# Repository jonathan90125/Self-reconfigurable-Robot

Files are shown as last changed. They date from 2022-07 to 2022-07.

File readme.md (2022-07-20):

# Self-reconfigurable Robot

## PHASE 1

This is the project I did for the "College Students Innovation and Entrepreneurship Competition" in China. And it was certificated as a province level project in the competition. 

### Background

Modular self-reconfigurable robots (MSRR) are robots that consist of many relatively simple individual robots which can cooperate together by changing their configuration according to different tasks. Many researches as shown below about this topic have been done in recent years, trying to achieve a practical robotic structure.  

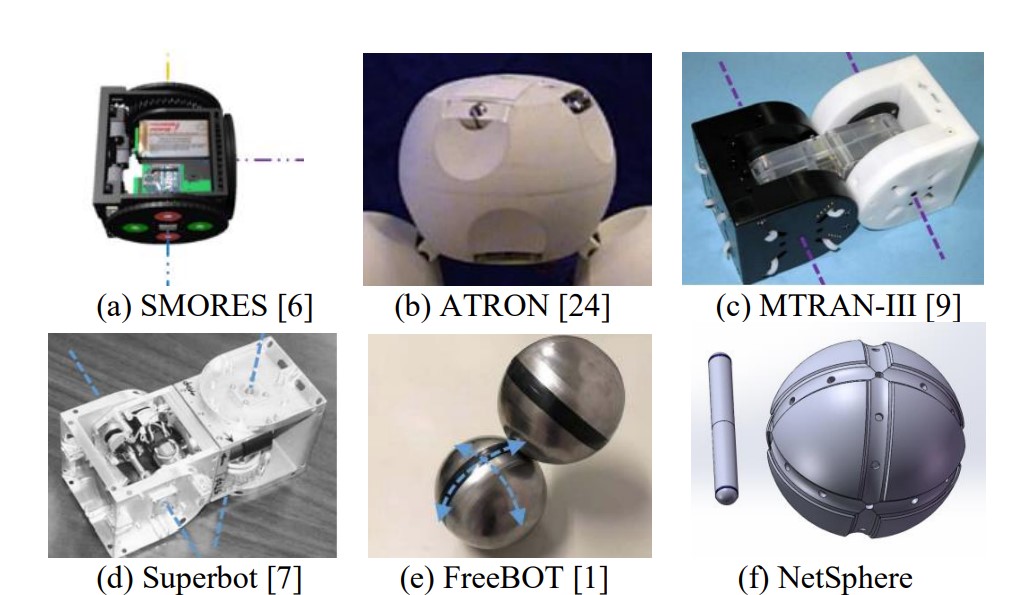
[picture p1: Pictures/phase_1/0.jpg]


### Introduction

In my opinion, former MSRR's major problem is the limited number of connectors on each individual robots. In order to solve that problem, I designed my own self-reconfigurable robot which contains two types of modules. The sphere modules can be connected by the stick modules to form various three-dimensional shapes. Sphere module contains ferromagnetic spherical shell and an internal actuating system. The remaining space in the shell can be used for electronic components and power supply (only one of eight sections is illustrated in the graph). An additional passive docking ports is on the shell which are used to cooperate with stick module. The stick module is equipped with two magnets and two active docking ports on both ends. The remaining space in the middle of the module is used for two motors which can actuate the docking ports. The internal  electronic components for each modules are very simple as shown in the graph below.

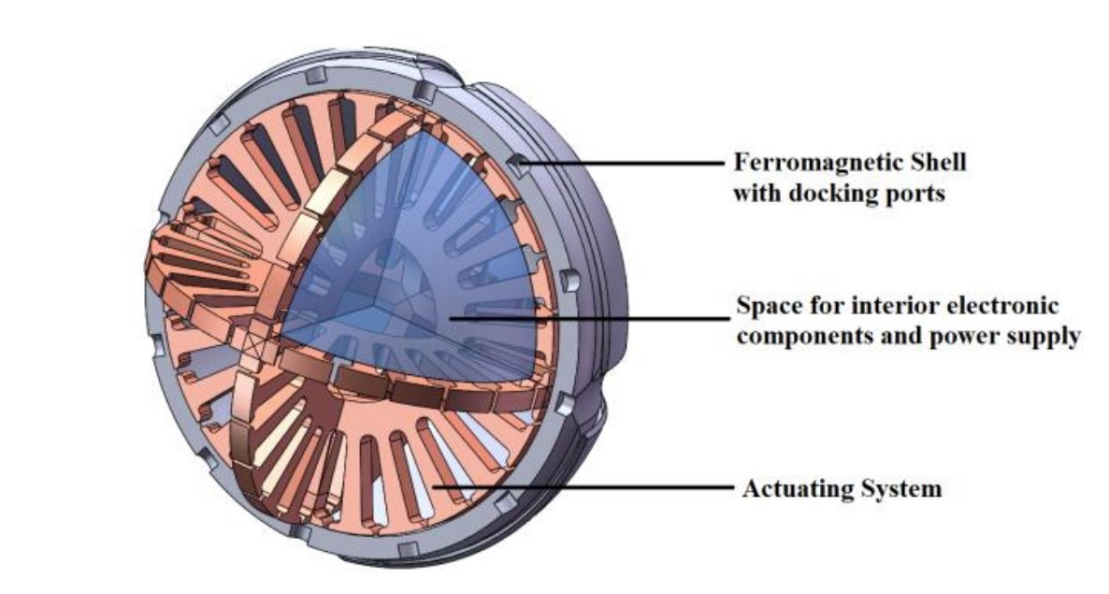
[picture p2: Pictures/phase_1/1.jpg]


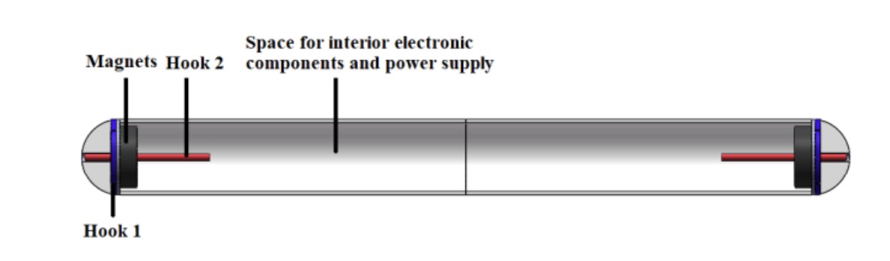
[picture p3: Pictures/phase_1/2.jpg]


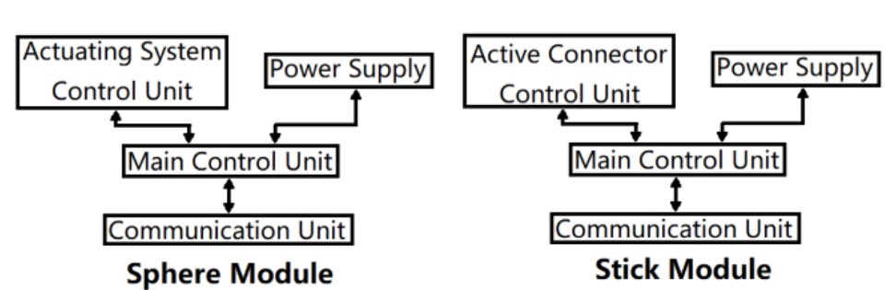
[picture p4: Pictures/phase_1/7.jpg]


### Actuating System

Figures below show the structure of the actuating system. There are three orthogonal circles inside the shell with 24 electromagnets on each circle, and each circle’s structure is similar to the stator of motor. All the electromagnets inside the sphere module are arranged  to control the magnetic force distribution of the spherical shell, which in turn can drive the magnets  at the end of the stick module to move on the surface of the sphere.

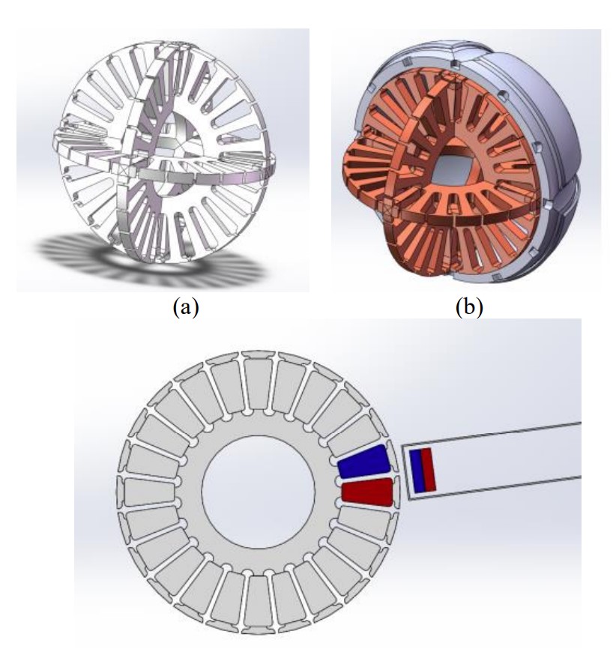
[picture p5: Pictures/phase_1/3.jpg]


### Docking System

There are two types of docking ports, the active docking ports of stick module and passive docking ports of sphere module. The hooks of active connector which is implemented inside the stick module have three states to provide suitable stability for the system. There are two different hooks in the active connector, one is to keep the stick module strongly connected to the surface of the sphere, the other is used to keep the stick locked at a certain position. There are three conditions of the two hooks, both nonactivated, only hook 1 activated, both activated, which means hook 2 can only be activated when 1 is activated. Hence, only one motor is needed to control both hooks since they are not independent.

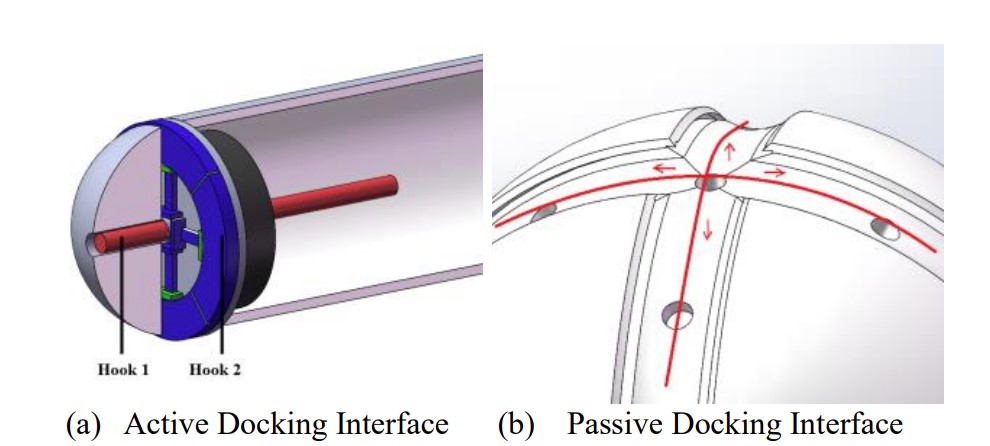
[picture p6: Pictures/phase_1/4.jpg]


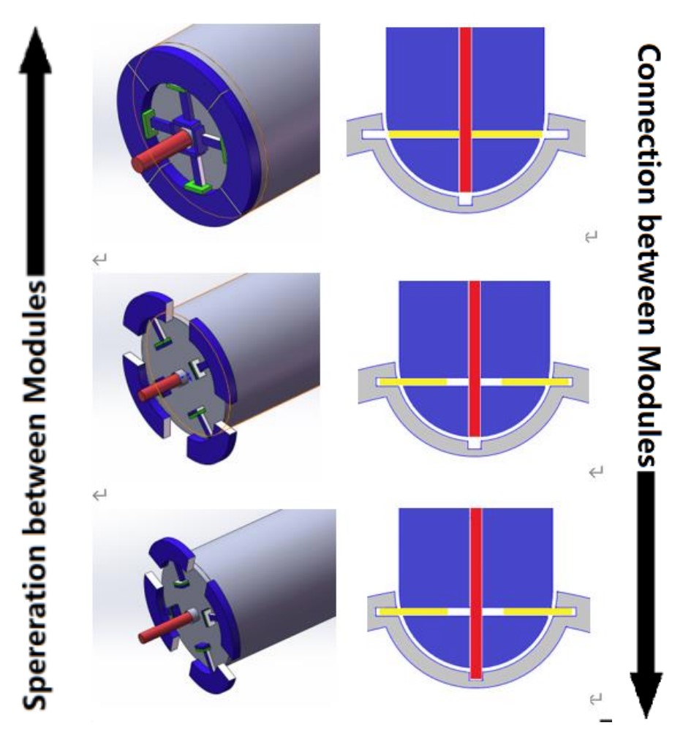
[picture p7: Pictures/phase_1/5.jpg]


### Connection of Individual modules

All the modules are meaningless unless they can cooperate together to form a holistic structure and solve problems cooperatively. So the algorithm to manage all the separate modules together to work together is also an important part of the design. Currently, the proposed strategy of connecting all the modules together can be arranged into 4 phases:

*1)*   *To from the simplest structure that is able to move independently. (a)*

*2)*   *Using these structures to gather more modules to achieve a relatively stable system. (b)*

*3)*   *Using the small systems that have been formed to gather modules. (c)*

*4)*   *Combining all the small systems together to obtain the final structure we desire.* 

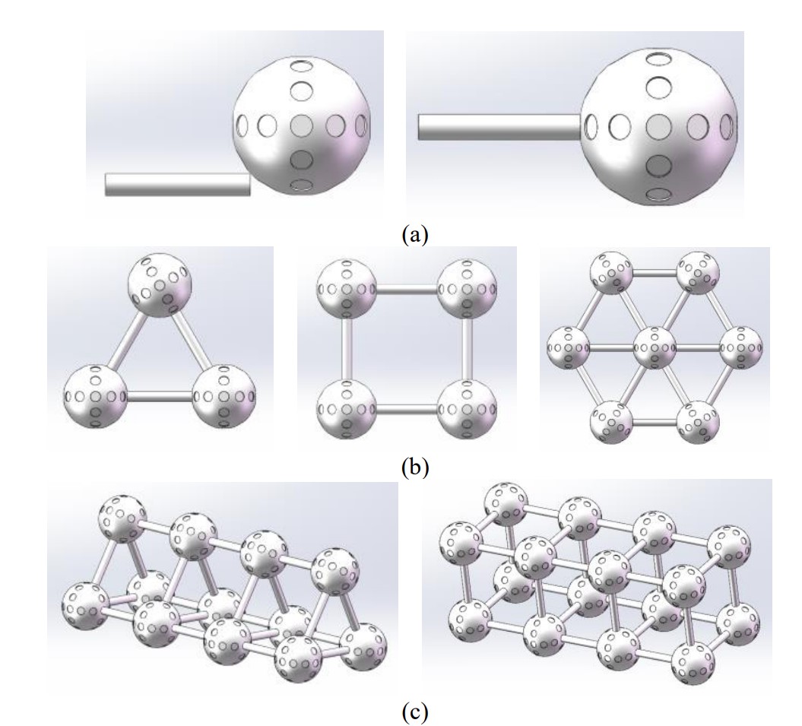
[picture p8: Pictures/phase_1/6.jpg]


### Implement

Some basic tests have been implemented to verify the feasibility of the actuating mechanism. Since the whole structure can be considered as three orthogonal stators and the electromagnets on each stator have little influence to other stators, the feasibility can be test on just one stator. A very preliminary experiment's devices are shown in figure below. The iron core of the prototype is using a stator which is made for motor. Its diameter is 40mm, height is 20mm, number of slots is 12. The diameter of varnished wire is 0.21 which could be much smaller to improve the performance significantly. Since the power dissipation can be reduced because no extra resistance is needed to constrain the current any more. On each tooth of the stator, we put an independent coil on it. The electronics in this testing device is very simple, using a STM32F103C8T6 to control all the independent coils, a ZigBee module CC2530 to communicate with upper computer. Some resistance is added to restrain the current inside the coil. A 12v battery is used to provide power for the coils. A voltage stabilization module AMS1117 is used to provide 3.3v power source for controlling circuit. A simple upper computer program has also been written to control each coil. 

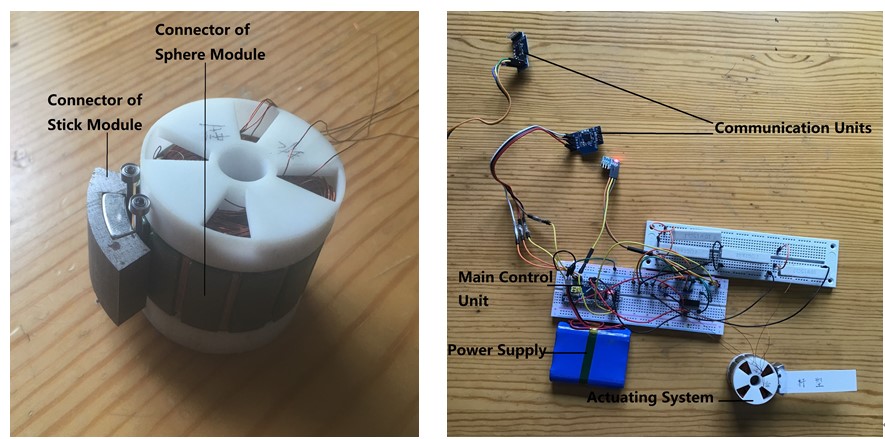
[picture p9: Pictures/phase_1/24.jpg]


## PHASE 2

Further development is carried out during my internship at CUHK's AI and Robotics laboratory. I made modification to the structure and made a functional prototype.

### Modification

The previous mechanical design is very difficult to manufacture especially the array of numerous electromagnets inside the sphere modules. Moreover, the torque provided by the actuator is limited and the connection between modules is not stable enough. To solve these problems, a modification for physical structure is necessary. 

The changed design is much simpler than previous one actually, the sphere module becomes just a hollow ferromagnetic ball and the stick module becomes what shows below. Two driving wheel and an array of magnet on each end and corresponding actuator and other units in between. And these modules can cooperate as shown below to form different shapes.

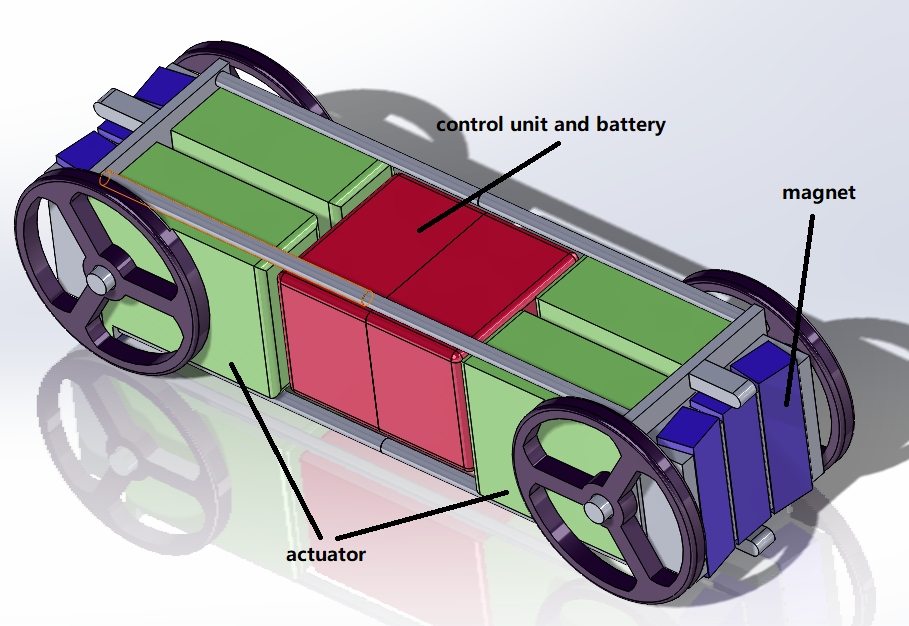
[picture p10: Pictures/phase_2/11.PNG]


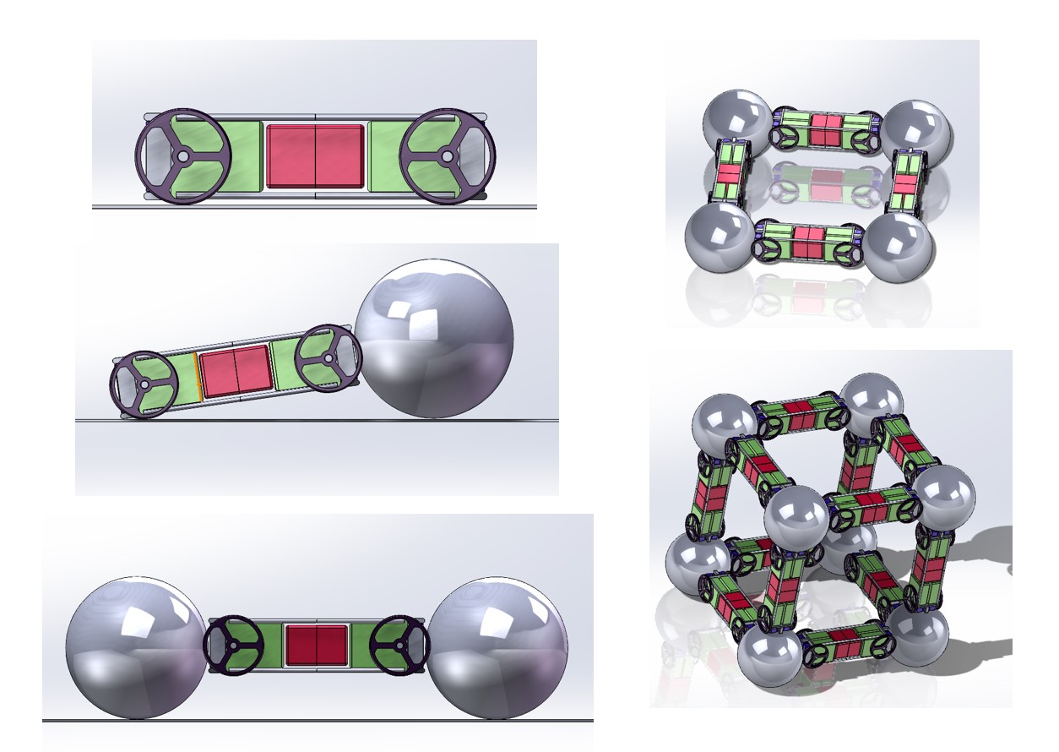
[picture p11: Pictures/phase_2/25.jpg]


### Implement

I firstly made a prototype using 3d printing to get all the components and the attached the wheels, motors and electronic units to it. This prototype can move independently on the ground with just one stick module and two sphere modules. 

After that I optimize the structure by using driving gears to minimize the size of modules. It can be seen that in the following figures, the size has been significantly reduced. 

After all these work, limited by the budget from the lab and I was arranged to other project (an AGV), I didn't make further development for the robots. 

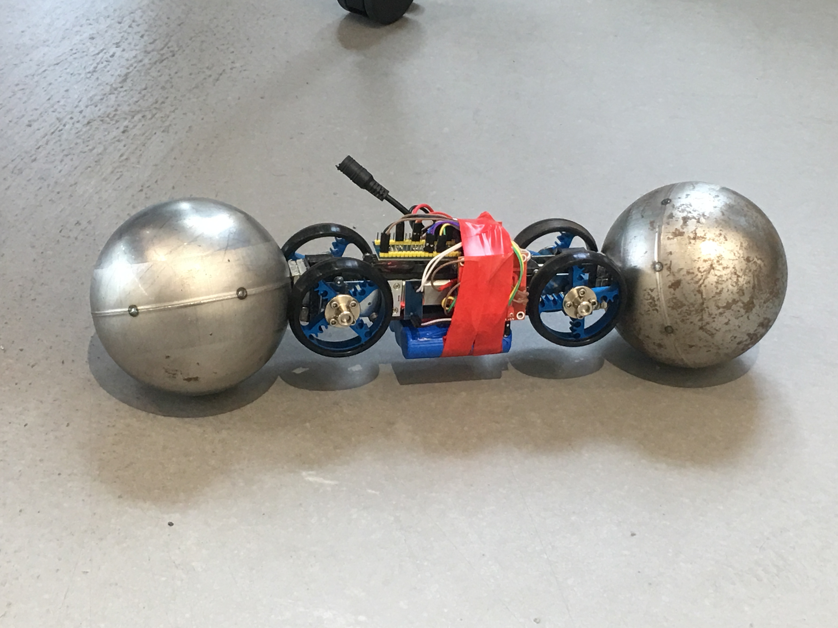
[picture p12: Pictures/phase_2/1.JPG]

<div align=center>
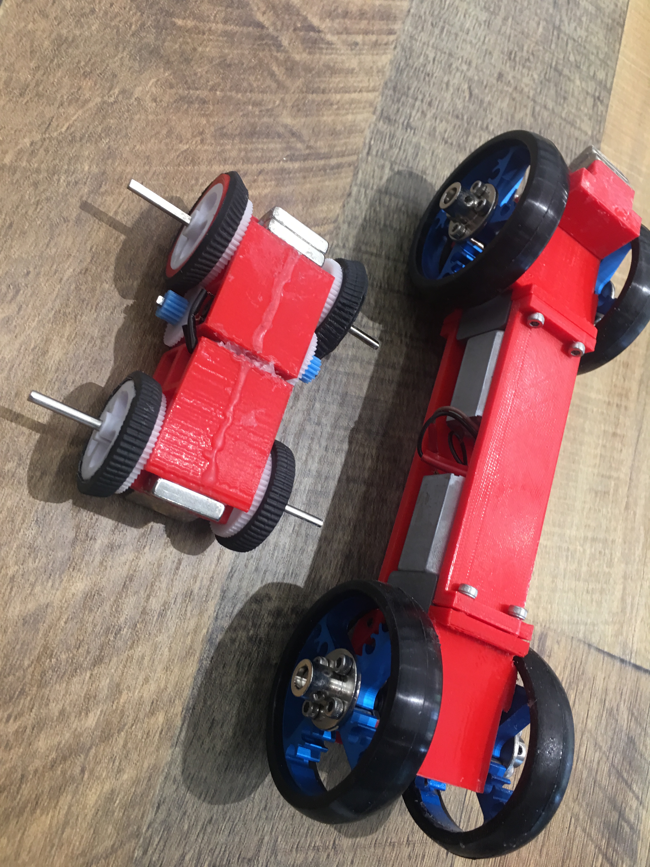
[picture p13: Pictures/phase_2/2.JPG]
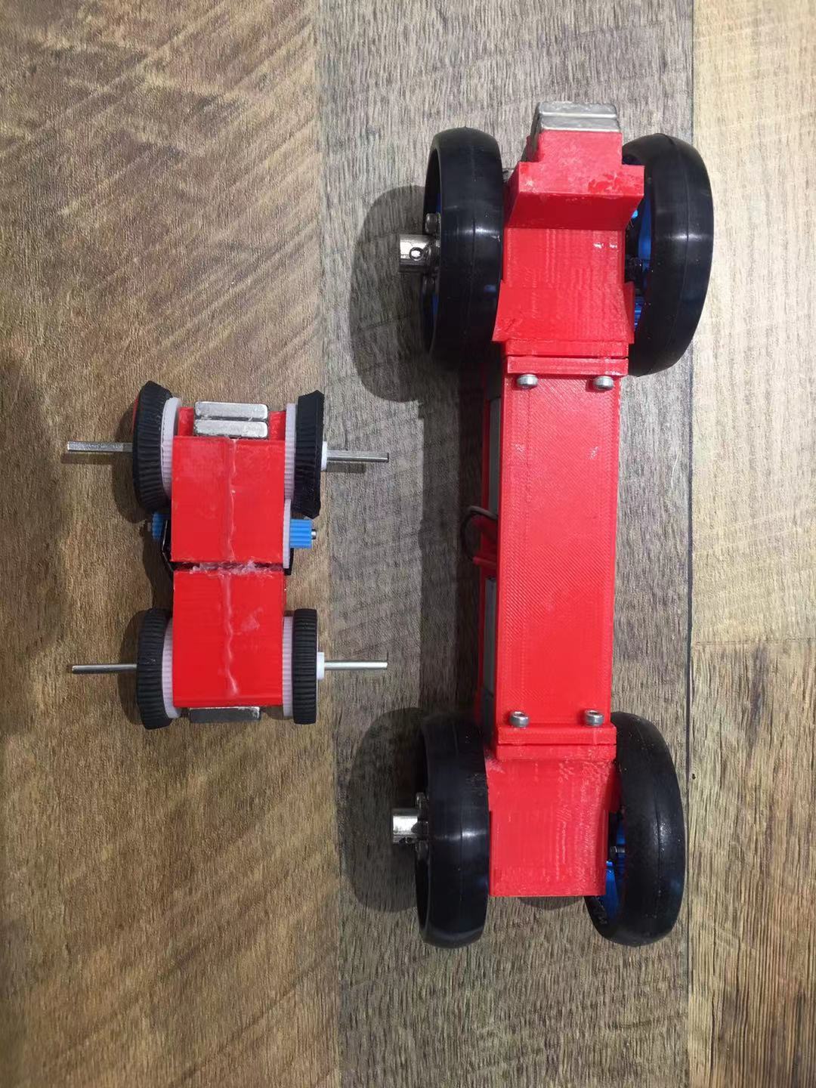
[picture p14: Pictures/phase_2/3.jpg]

</div>
<div align=center>
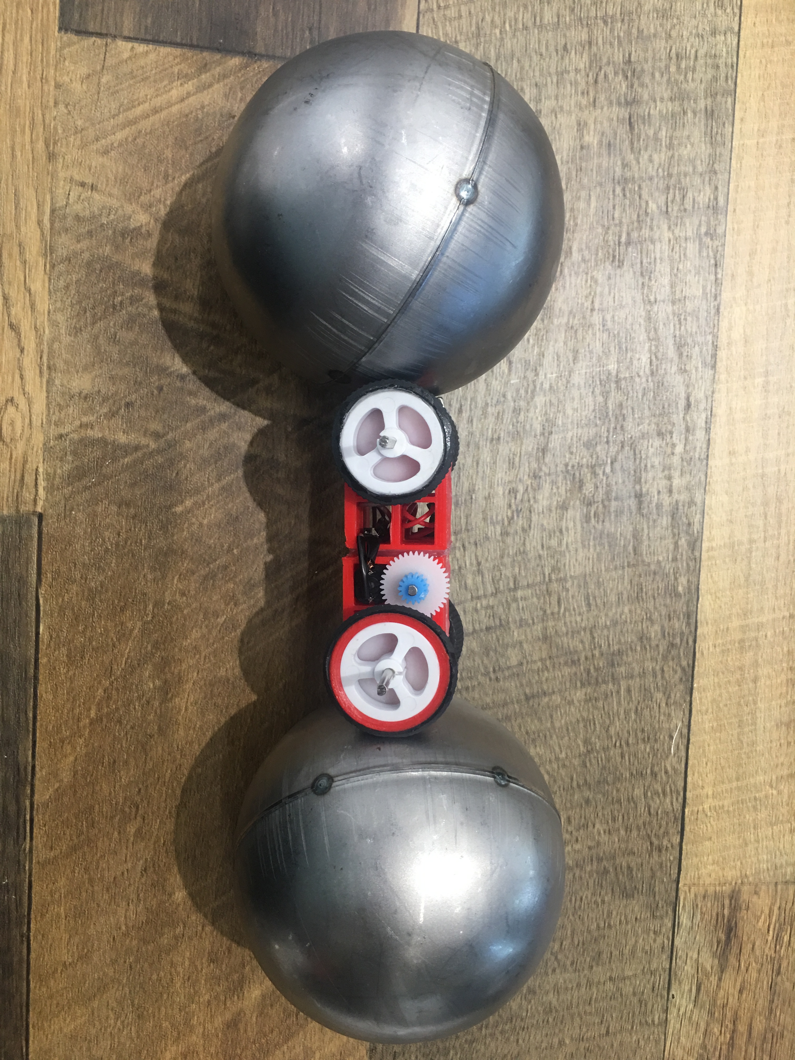
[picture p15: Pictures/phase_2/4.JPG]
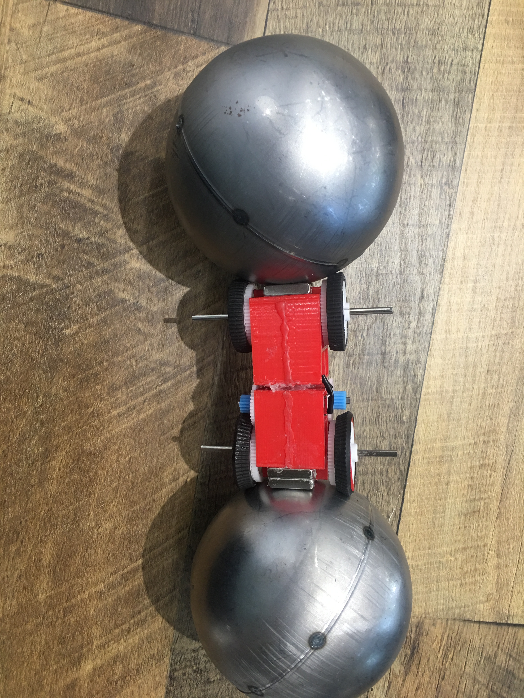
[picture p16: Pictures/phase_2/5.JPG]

</div>

## Future Work

What I was trying to achieve has been implemented by a team from CUHK(Shenzhen) as shown in figures below, details can be found in the paper "FreeSN: A Freeform Strut-node Structured Modular Self-reconfigurable Robot - Design and Implementation". The mechanical design is basically the modification version in phase 2 I illustrated above. In fact, I was working at CUHK(Shenzhen)'s AI and Robotics laboratory at that time when that team is working on this project. I met some members of the team who are also reviewer of my paper that I wrote in phase 1, they gave me some very helpful advice like using simulation to prove the feasibility of the design. But, when I mentioned I was trying to make some modification on the design of the self-reconfigurable robot later, they were doing the similar work simultaneously. They insisted that this was their original idea and they have proof for it.  

Apparently, their prototype is much more elegant and compact than mine. I'm very glad that this idea could be implemented even though not by myself. Since currently the physical prototype has been made, the corresponding controlling algorithm  should to created in the future. Moreover, the size should be minimized and the torque provided by the actuator should be enhanced. 

In my future work, I would like to focus on the controlling algorithms of multi robot instead of innovation about physical structures. Task decomposition, coalition formation and task allocation of multi robot could be interesting researching areas.  

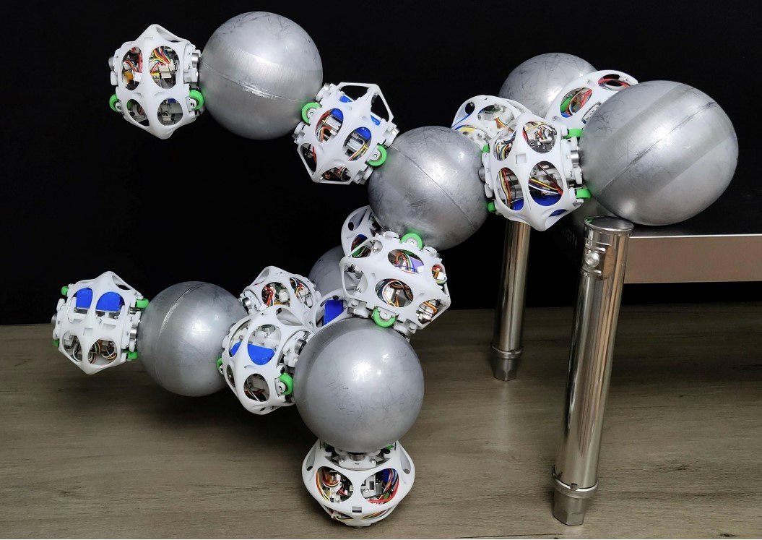
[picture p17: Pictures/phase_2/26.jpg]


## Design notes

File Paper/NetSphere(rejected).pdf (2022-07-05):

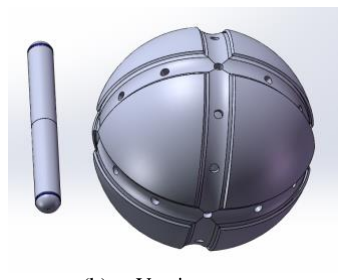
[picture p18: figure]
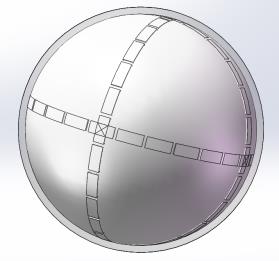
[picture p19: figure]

Abstract—In this paper, a novel design of lattice-like modular self-reconfigurable robot named “NetSphere” which does not apply traditional motor as its actuator will be described. The module of NetSphere can actuate its adjacent module by altering the magnetic force distribution of the spherical shell which is achieved by manipulating the interior electromagnet. There are two versions of designs with different advantages. Version one NetSphere is more likely to realize a freeform robotic system without the constrain of physical connectors. Version two NetSphere is equipped with physical connectors which leads to a more reliable system with large holding force. Both versions of design are capable of the basic functions that achieved by previous MSRRs like connection and separation, 3D reconfiguration. Moreover, with the innovative actuating mechanism, NetSphere can handle much more connectors simultaneously than previous design which increase the versatility and flexibility of the system significantly.

I. INTRODUCTION
odular self-reconfigurable robots (MSRR) consist of many relatively simple individual robots which can cooperate together by changing their configuration according to different tasks. Many researches about this topic have been done in recent years [1]-[5], trying to achieve a practical robotic structure. Multiple MSRR modules forming joints are the main self-reconfiguration method of most MSRR systems in previous research. Moreover, most former designs, such as SMORES [6], SuperBot [7], PolyBot [8] and M-TRAN [9], [10], have to use a motor for driving each joint, which means the robotic system’s degree of freedom (DOF) depends on the number of motors. Therefore, to realize a robotic system with high flexibility, the interior space used to place motors and its corresponding drive system will be very large. In addition, if the system is applying physical connector, such as Sambot [11], Roombot [12] and M-TRAN [9], [10], each independent control on a specific connector requires a motor as well. Since the interior space in an individual robot is limited, the DOF and number of connectors are restricted as well.
However, a recent research FreeBOT [1] proposed a new design that each robot can freely attach to any other robots at any point. FreeBOT is mainly composed of two parts: a spherical ferromagnetic shell and an internal magnet. By changing the location of the magnet on the shell, magnetic

Xinzhuo Li is with Beijing Jiaotong University, Beijing,100044 CHINA. (e-mail: 18722012@bjtu.edu.cn).
Hang Zhou, Dr., is with Beijing Jiaotong University, Beijing,100044 CHINA. (e-mail: hangzhou@bjtu.edu.cn).

force distribution of the sphere surface is transformed to alter the connecting condition between robots.
The maximum number of motors in an individual robot did not exceed 10 in any previous researches. This is reasonable because the interior space of robot is limited. One of the key topics of MSRR in previous research is to find how to arrange these limited motors to actuate the entire system. For example, SMORES [6] uses gear train to let 4 actuators cooperate together for the reconfiguration of robots and utilizes permanent magnets as the connectors, which leads to high DOF and weak holding force. Meanwhile, Sambot [11] allocate more actuators for its physical connectors with hooks to achieve a stable connection. In addition, unique design like M-block [13] was also proposed, which used a powerful actuator to drive the flywheel inside the robot in order to make the robot rotate. The structure of M-block is very simple and compact, but the robotic system is very unstable because of the flywheel.
Although, FreeBOT is still using motors to actuate the wheels to drive the magnet, the essential actuating strategy has changed. Previously, any movement of connectors on the robot surface is directly driven by a motor, which means it can only be a one-dimensional transformation which indicates the connector can only either rotate or expand. However, FreeBOT actuates its connector by changing the magnetic force distribution of the sphere surface. By changing the state of the spherical surface instead of a single connecting point, FreeBOT achieved a two-dimensional transformation at any point on the surface of the robot. The change is achieved by using two cooperating motors to drive the magnet inside the shell, which indicates it can only realize one free connecting joint on its surface.
However, there are nonnegligible drawbacks of FreeBOT as well. Each robot can only have one connector. For example, if FreeBOT forms several chain-like structures, then each

## NetSphere: Design of Modular Self-reconfigurable Robots with a novel actuating mechanism

Xinzhuo Li and Hang Zhou

M

(a) | Version one | (b) | Version two

Fig. 1. Novel MSRR designs - NetSphere chain cannot connect to each other, since all the connectors have been used to maintain the chain. Moreover, most of the interior space are wasted to lower the gravity center and the holding force in tension is relatively small.
This paper proposes a novel MSRR design called NetSphere, which implements a new actuating mechanism without using motor. NetSphere applies the same actuating mechanism as FreeBOT which is changing magnetic force distribution of the sphere surface to drive the adjacent
modules. | NetSphere | is | constructed | with | discrete
electromagnets inside the shell instead of single moving magnet, which solved all the problems about FreeBOT mentioned before. Although NetSphere is not able to achieve connection on any point of the shell comparing to FreeBOT, it increases the number of connectors significantly, and the all of them can be actuated simultaneously.
This paper proposes two versions of design about NetSphere (as shown in Fig. 1). The difference of them is their docking system. The first design functions similarly to FreeBOT, but with restricted connecting points. The second design consist of two types of modules, the sphere module and the stick module. This design achieved physical docking ports and reduce the cost of realizing a same volume system. Both designs are able to replicate all the basic functions of previous MSRRs except independent movement. The reason of designing two versions of NetSphere will be discussed in the Section III.
This paper is organized as follows. Section II describes the mechanical design. Section III compares two versions of NetSphere. The motion of NetSphere and experiment results are introduced in Section IV and V respectively. Section VI compares NetSphere with the currently most advanced MSRRs. Finally, conclusions and future work are given in Section VII.

II. MECHANICAL DESIGN
Mechanical design mainly focuses on the actuating system and the docking system. Both versions of NetSphere’s mechanical design will be introduced
A. Module Design
Fig. 2 shows the interior structure of both versions of NetSphere. Version one module is mainly composed of two parts: a ferromagnetic spherical shell and an internal actuating system. The remaining space in the shell can be used for electronic components and power supply (only one of eight sections is illustrated in the graph). Version two NetSphere consists of two types of modules. As illustrated in (b), sphere module is similar to version one module. The only difference is the additional passive docking ports on the shell which are used to cooperate with stick module. In (c), the stick module is equipped with two magnets and two active docking ports on both ends. The remaining space in the middle of the module is used for two motors which can actuate the docking ports. Electronic components and power supply are placed here as well. Detailed structural diagram of version two NetSphere is shown in fig. 3. Different types of modules’ general structures are similar. They both consist of a main control unit to manipulate other units, a communication unit to communicate with other robots and upper computer and a power supply. The only difference is the control unit for their unique components. For sphere module, the control unit needs to manipulate 30 electromagnets simultaneously. For stick module, the control unit needs to choose the correct docking condition for the active connector. The structure of NetSphere is very simple and compact which indicates great potential for micromation.

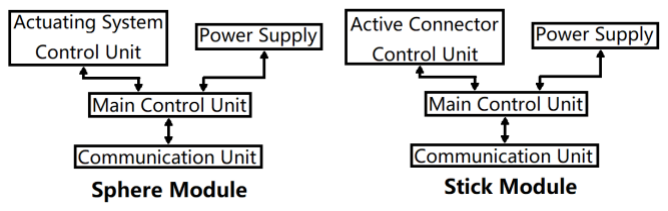
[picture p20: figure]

B. Actuating System
Fig. 4(a)(b) show the structure of the actuating system of the NetSphere for both versions (coils are hidden to keep the figure clear). This is fundamental part of the whole design.

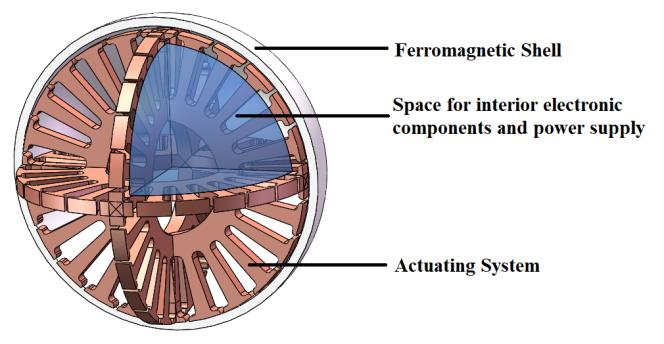
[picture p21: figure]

(a) Version one

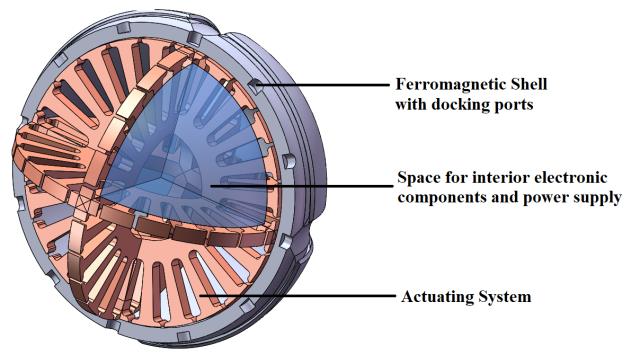
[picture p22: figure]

(b)Version two-sphere module

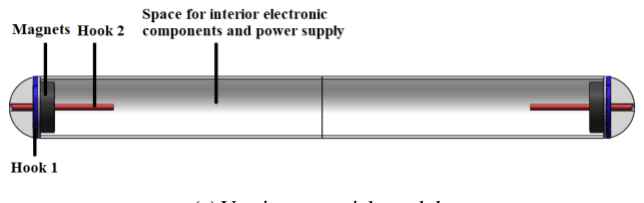
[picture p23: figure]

(c) Version two-stick module
Fig. 2. Design of the Module Interior Structure

Fig. 3. Structural diagram of Version two NetSphere

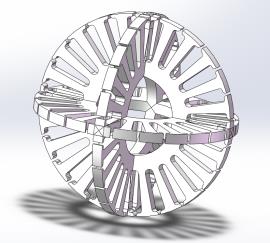
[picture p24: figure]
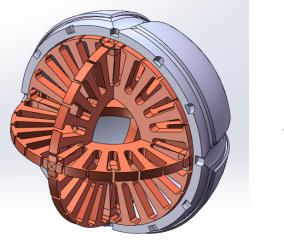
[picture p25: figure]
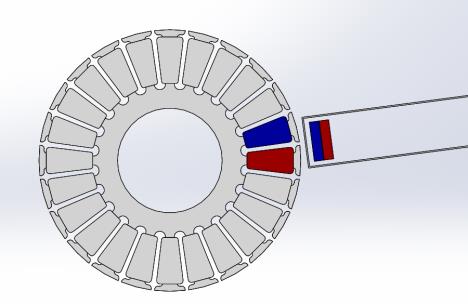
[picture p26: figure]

Before delivering the detailed description of actuating system, the initial idea of the structure will be illustrated. The intuitive modification of FreeBOT is to directly using electromagnet inside the sphere to change of magnetic force distribution of the sphere surface. However, no matter how we arrange the structure of the electromagnets, this will lead to discrete points on the surface. An approach to solve this problem is to implement numerous enough points to realize an approximate performance like FreeBOT, which is not feasible at present. In fact, even FreeBOT’s movement is discrete since the motor can only rotate a minimum angle because of the number of stators and rotors in the motor is limited, hence there will be a minimum step for FreeBOT to move. Therefore, how to arrange the distribution of electromagnet inside the shell becomes the key problem.
Mainly two methods to arrange the points on the surface of a sphere are taken into consideration. First is to consider a sphere as a polyhedron, and the vertices of the polyhedron are placed with docking ports and corresponding electromagnets. There are only five types of polyhedron in the world whose number of vertices are 4,6,8,12,20. This method can equally divide the surface, but it will result in too much constrain on the movement between vertices. For example, except octahedron, if a connector is keeping moving from one vertex to an adjacent vertex, the connector cannot keep its original direction. Second is to utilize the model of latitude and longitude, this method solves the direction problem perfectly since the surface is occupied by orthogonal points of two circles. However, with same longitude difference, the distance between two points at higher latitude is much smaller which leads to collision of connectors.
Therefore, the ultimate design that we chose is three orthogonal circles on the surface of the sphere with 24 electromagnets on each circle. Because for version two NetSphere’s sphere module, each passive docking port requires two corresponding electromagnets. And if the system is able to achieve basic two-dimension configuration like triangle and rectangle, at least 12 docking ports is the necessary requirement for a circle. This structure is a combination of two previous methods. It can be considered as an octahedron with divided edges or a simplified model of latitude and longitude.
Fig. 4(c) shows that each circle’s structure is similar to the stator of motor. From this perspective, the actuating system can also be considered as three orthogonal motor stators. But each tooth of the stator is controlled independently, this tradeoff is to achieve more flexible transformation with less torsion of a same size motor which is key novelty of the actuating design. However, since the ‘motor’ inside NetSphere has almost the same diameter of the robot, it must be relatively larger than motor inside other same size MSRR modules. Therefore, the torsion and holding force provided by the actuating system is considerable. Moreover, different ‘tooth’ can cooperate together to achieve stronger torsion, which will be discussed in the Section IV.
Although two versions NetSphere uses the same actuating system, the operating mechanisms between them are totally different. Version one NetSphere function similar to FreeBOT, the module rotates because the adjacent electromagnet is activated and trying to attach to the ferromagnetic spherical shell of the other module. On the other hand, version two NetSphere function like a Brushless DC Motor. The magnet inside the stick module can be considered as a part of the rotator and the electromagnets inside the sphere module can be considered as part of the stator. At different time of the operation of the brushless motor, each magnet of the rotator is repelled or appealed by some specific corresponding electromagnets of the stator according to the program. Therefore, we can activate the corresponding electromagnets inside the sphere module to actuate the magnet inside the stick module on different position of the shell. Moreover, the structure of iron core illustrated before is only a primary example to illustrate the actuating mechanism, the optimal and practical shape design in our future work can be improved based on the previous research about the analysis of Brushless DC Motor. For example, in [14], the author delivered the analysis of the behavior of motor during commutation, including output waveform for current, back EMF, speed and torque. And commutation plays a significant role in the process of actuating system’s operation. Therefore, this paper will be of
(a) (b)

(c)
Fig. 4. Actuating System

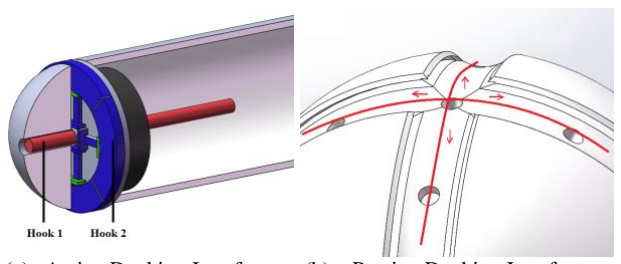
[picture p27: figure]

(a) Active Docking Interface (b) Passive Docking Interface Fig. 5. Docking Ports

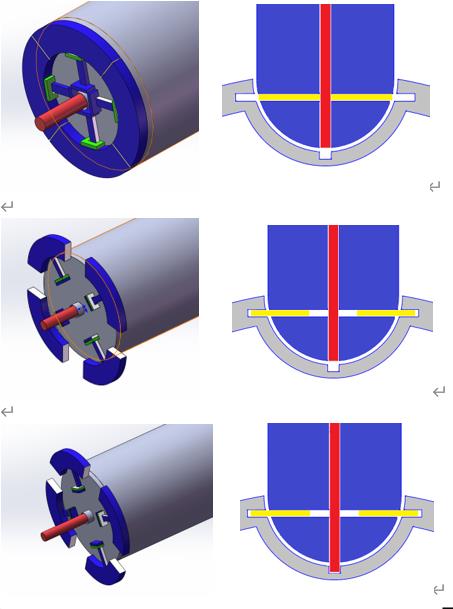
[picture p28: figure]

great use for implementing the control algorithm for actuating system.

C. Docking System
The version one NetSphere’s docking system is the same as FreeBOT, which is using magnetic connection. Therefore, this part will mainly focus on the docking system of version two NetSphere.
A significant difference between version two NetSphere and previous MSRR is that NetSphere has two types of modules. The reason of this will be discussed in Section III. This part only describes the docking mechanism between two types of modules.
The docking mechanism is one of the most important and popular topics of MSRR research and many innovative designs have been illustrated in previous research. For example, the hooks that are activated by DC motors [9], [10], [12], [15],[16] permanent magnets [6], electromagnets [13], [17], or electro-permanent magnets [18]. In [19], the author proposed the concept of “the area of acceptance” for MSRR, which is defined as “the range of possible starting conditions for which mating will be successful”. The author also indicated that proper connectors can save resources such as space and power for the modularized system. Connector with a larger area of acceptance is more likely to succeed when connecting. Generally, physical connectors like hooks activated by DC motor can achieve strong connection but the connecting success rate is relatively low, because it has a small acceptance area. On the other hand, magnetic connectors like permanent magnets or electromagnets have large acceptance area but cannot be strongly connected. This paper proposes a novel docking mechanism to achieve both a strong connection and a large acceptance area. The reason that NetSphere can achieve advantages of both docking mechanism is that the connector can function using merely magnetic connectors, without using the physical connectors. The ferromagnetic shell of the sphere module and the magnet inside the stick module provide enough connecting force. The physical connectors are added to obtain strong connection and lower power consumption which are both very important in MSRR system. Fig. 5. Shows the active docking ports of stick module and passive docking ports of sphere module. The hooks of active connector which is implemented inside the stick module have three states to provide suitable stability for the system. There are two different hooks in the active connector, one is to keep the stick module strongly connected to the surface of the sphere, the other is used to keep the stick locked at a certain position. There are three conditions of the two hooks as shown in Fig. 6, both nonactivated, only hook 1 activated, both activated, which means hook 2 can only be activated when 1 is activated. Hence, only one motor is needed to control both hooks since they are not independent. A strong permanent magnet is installed at the bottom of the stick to create strong connecting force and driving force. The active connector is placed in both of end of the stick module. The passive docking ports are all on the shell of sphere module. Although the sphere module can connect 30 active connectors at the same time, all the passive connectors are organized together as a highly compact entirety. The passive connector consists of two kinds of cavity for each hook. By separating passive and active connectors into different types of modules, the structure of the system can be kept simple and compact.
In [20], the author delivered two concepts, “Degree of
Reconfigurability | (DOR), | the | number | of | possible
combinations with the number of modules”, and “Integrity, the quality of integration”. Every modularized system has to deal with the inherent trade-off between DOR and integrity. In this paper, the author proposed that applying genderless connectors can compensate for the degradation of integrity when increasing the number of connection ports and the kinds of module. Although the system using male-female latches between two types of modules, if we consider the stick modules only as the ‘connectors’ between sphere modules. The connection between different individual sphere module is actually genderless. The reason that genderless connectors have better performance is that when arranging the structure of MSRR with gender-opposite connectors [16], [17], [21], [22], [23], we not only need to consider the position of different modules but also need to ensure that the adjacent connectors are gender-opposite. However, since the connectors between different types must be gender-opposite, the ‘connection’ of two module of same type will be genderless. And the stick module is determined by the structure of sphere module. When we arrange the structure of the whole system, we can assume that the system only consists of sphere modules and has gender-less connectors which is very helpful for designing motion planning algorithm.
As shown in Fig. 7, the inside driven mechanism of stick

Fig.6. Connection and separation between Modules

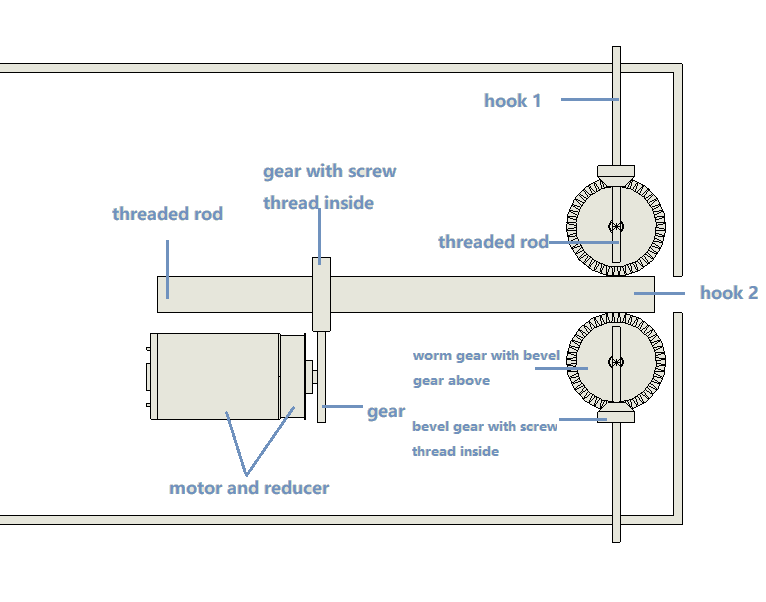
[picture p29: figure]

module is as follows: the output of a micro DC motor is decelerated by a pair of gears, and then, transmitted to the threaded rod which also function as the hook 2 of the active docking port. The threaded rod can move horizontally in the graph, which will drive four worm gears (only two are illustrated in fig. 7.) connecting to it. When the worm gear with bevel gear above rotates, it will drive the adjacent bevel gear with screw thread inside which will drive the threaded rod used to actuate hook 1. Hook 1 will expand to the functioning position before hook 2, although additional space in passive docking port for hook 1 is needed during the process when hook 2 expand to the proper position. Therefore, only one motor is need for each active connector to achieve three conditions.

III. COMPARISON BETWEEN TWO VERSIONS OF NETSPHERE
There are several differences between two versions of NetSphere even though their actuating systems are identical. The biggest difference is version two consists of two types of modules. There are three reasons. First is to increase the number of connectors. The maximum number connectors will increase when we add a line whose length is the diameter of the circle between two circles. The second reason is to apply physical connectors to increase the holding force. And the application stick module also leads to genderless connection between sphere modules. The third reason is to reduce the cost. Because the stick module is much simpler and cheaper than spherical module, using stick module can achieve a same volume system with much lower cost. Therefore, version two NetSphere generally have better performance than version one. However, version one has some nonnegligible advantages which make this design be introduced in this paper. Firstly, without considering actuating system inside the shell, the connecting points can be anywhere on the shell instead of just the three circle orbits. Moreover, the structure of actuating system has a potential to change into any form instead of what has been described in section II. Because without the restriction of discrete physical connectors, the arrangement of electromagnets in the shell could be more flexible. For example, the method that implementing numerous enough points to realize an approximate magnetic force distribution of the sphere surface like FreeBOT which has been mentioned before could be possible for version one NetSphere. Hence, version two NetSphere is a more feasible and reliable design currently, but version one NetSphere has great potential to realize a freeform robotic system.

IV. MOTION
The motion of version one NetSphere will not be discussed in this section because its motion is very similar to FreeBOT which has been well illustrated. This section will mainly focus on the motion of version two NetSphere.
A. Independent Motion
The individual module of version two NetSphere cannot move on its own no matter what type it is in the ordinary circumstance. However, if a ferromagnetic plane is provided, the sphere module can function similarly to FreeBOT, and it can climb on a ferromagnetic wall too. The simplest combination of modules that can achieve independent motion is a single sphere module and a single stick module. the stick module can rotate around the circle to push this simple system forward.
B. Connection and Separation
Fig. 8 from (a) to (c) shows the connection between two types of modules. The sphere module activates the electromagnets near the stick module. Then slowly slides the window of activated electromagnet to make the stick perpendicular to the surface to achieve a stable latch. Then the connector can rotate around the circle orbit or change its direction to other circle orbit at the intersection. The separation is much simpler comparing to connection, just need to let all the electromagnets near the stick module repel the magnet inside it. Since the sphere modules are equipped with ferromagnetic shell, the magnet at the end of the stick module can provide enough connecting force without using the hooks. The hook 1 can be activated to increase the stability, and hook 2 can be activated to lock the connector at a certain position. However, neither of the two types of modules can keep its original pose and orientation during this connecting process. Moreover, if they are not close enough, the connection will be impossible

Fig. 7. Drive System of Active Docking Ports

(a) (b)

(c)
Fig. 8. Connecting Process between Two modules because separate individual module cannot achieve independent motion. Hence, this process has a high possibility to fail. But, if several modules have been connected together, using this existing system to connect other modules will be much easier. Because the stability of existing system is utilized to make the sphere modules have better control of the stick module that is connecting to it or will be connected to it. Moreover, the connection between two existing system will be much easier as well.
Therefore, the strategy of connecting all the modules together can be arranged into 4 phases:
1) To from the simplest structure that is able to move independently. (Fig. 9.(a))
2) Using these structures to gather more modules to achieve a relatively stable system. (Fig. 9.(b))
3) Using the small systems that have been formed to gather modules. (Fig. 9.(c))
4) Combining all the small systems together to obtain the

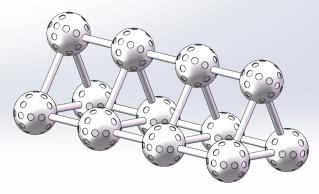
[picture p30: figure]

final structure we desire.

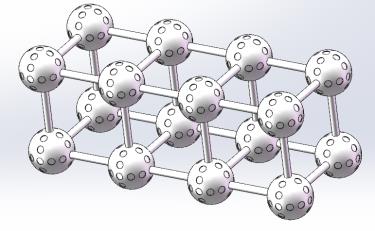
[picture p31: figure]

From 1 to 4 the stability and robustness of the system increase significantly, and the connecting process between modules will have higher success rate and faster speed. Therefore, the system consisting of higher rank component will have better performance. by using physical latches, NetSphere can maintain all the connection without power consumption. This enables the system to skip previous phase of assembly and start with higher-level components at the beginning of the task. This also indicates that the MSRR system should maintain relative higher-level components instead of decomposing to separate individual modules after accomplishing the task and powering off.

C. Reconfiguration
The most significant problem of MSRR system is how to achieve cooperation between a larger number of modules.

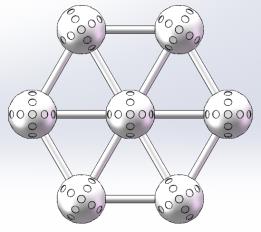
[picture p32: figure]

Comparing to tradition robots, the force that an individual module can provide is very limited because of its simple structure and small volume. Therefore, it is necessary for the modules to cooperate together to achieve a stronger force. All torsion in the system that is provided by the sphere module to make its adjacent module rotate around it. From this point of view, the connection between two sphere modules can be considered as a joint. The method to unite all the torsions is to make them related to the same axis. This method applies to all the MSRR systems that using joints to connect modules. There are two ways of NetSphere to realize this effect as shown in Fig. 10. First is to combine all the modules that connecting to a single sphere module’s same circle orbit. The second is to combine all the parallel stick modules together. These two methods also indicate why the electromagnet structure is three orthogonal circle. Since rotation is the only transformation form in this MSRR system which is a two-dimensional transformation, a circle orbit to implement this kind of transformation is necessary because a circle orbit has no constrain for the rotation process. The circle orbit determines a plane, and in order to combine different torsion in different planes, all the planes should be parallel to each other. Hence, the connection between two cooperating planes of modules must be perpendicular to both of the planes. The specific connecting locations is exactly at the intersection points of the other two circle orbits on the spherical surface. This is actually the most important reason that leads to the final structure of actuating system.
Therefore, | the | reconfiguration | of | NetSphere | in
two-dimension is very flexible, and the three-dimensional structure can be considered as a combination of many layers. In addition, this is certainly not the only 3D structure that NetSphere can form. However, since this is highly related to the reconfiguration and motion planning algorithms which is not the key topic of this paper, other forms of 3D reconfiguration will not be discussed in details.
V. EXPERIMENT AND RESULTS
The most significant design of NetSphere is the actuating mechanism. Therefore, some basic tests have been implemented to verify the feasibility of the actuating mechanism. And the testing device performance data has been shown in TABLE I. Since the whole structure can be considered as three orthogonal stators and the electromagnets on each stator have little influence to other stators, the feasibility can be test on just one stator. This modification significantly simplified the structure of the prototype and enabled us to implement some basic experiments in the early

Fig. 10. Two methods to strengthen the system

(a)

(b)

(c)
Fig. 9. Assembling Components from Different Phases

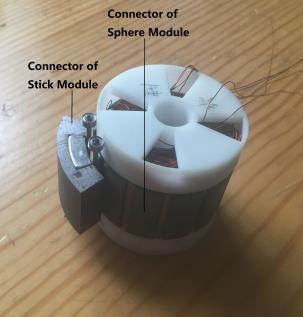
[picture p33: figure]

phase.

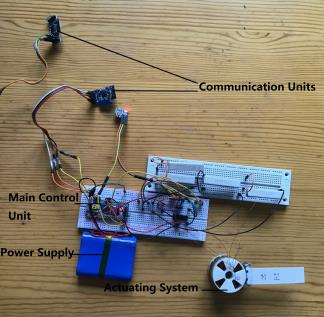
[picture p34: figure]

The experiment devices are shown in Fig. 11. The iron core of the prototype is using a stator which is made for motor. Its diameter is 40mm, height is 20mm, number of slots is 12. The diameter of varnished wire is 0.21 which could be much smaller to improve the performance significantly. Since the power dissipation can be reduced because no extra resistance is needed to constrain the current any more. On each tooth of the stator, we put an independent coil on it. The electronics in this testing device is very simple, using a STM32F103C8T6 to control all the independent coils, a ZigBee module CC2530 to communicate with upper computer. Some resistance is added to restrain the current inside the coil. A 12v battery is used to provide power for the coils. A voltage stabilization module AMS1117 is used to provide 3.3v power source for controlling circuit. A simple upper computer program has also been written to control each coil.
The magnet can change its position on the rotator by changing the distribution of activated electromagnets around it, but the joint doesn’t have very strong torsion because most of the energy is wasted by the resistance which are used to restrict the current inside the coil.
This is just a very preliminary experiment to test the feasibility of the actuating mechanism. The connection and separation of different modules, the reconfiguration of the whole system, can only be tested on a complete prototype. However, this simple experiment demonstrated the feasibility of the actuating system with a very low cost. And it consists of most of fundamental components of NetSphere, such as communication unit, main control unit, power supply and actuating system, which means the complete prototype will also have a low cost. And this is a significant feature for MSRRs to get mass production.

VI. RELATED WORK

This section will only focus on the version two NetSphere because two versions design have many common features when comparing to other MSRR. NetSphere is different from all the previous MSRR because of its actuating mechanism, the two types modules design and the novel docking mechanism.
However, NetSphere still can realize some common functions as previous MSRR like connection and separation between modules, system reconfiguration and movement. Using multiple modules to form joints is the main self-reconfiguration method of most MSRR systems. As showing in the figure, all the previous research except FreeBOT, joints in the system can only rotate around one axis, while the FreeBOT system can form an unlimited revolute joint. As for NetSphere, there are six points where joints are rotating around two axes, while at other places joint can only rotate around one axis. In any other previous research, there can only be one connector being actuated around an axis. But sphere module is capable of actuating 12 connectors on the same circle orbit simultaneously, which increases the versatility of the system significantly. As shown in Fig. 12. and TABLE II, NetSphere has a huge advantage in the number of actuators and connectors comparing to other MSRRs.
Moreover, any MSRR design has to deal with a difficult tradeoff between the flexibility and the connecting strength. Physical latches can greatly improve the holding force of the system, but they will lead to discrete physical constrain which will reduce the flexibility of the MSRR. However, NetSphere can achieve both a strong connection and a large acceptance
(a) (b)
Fig. 11. Experiment devices

TABLE I

ACTUATING SYSTEM TESTING DEVICE PERFORMANCE DATA

Specification | Value
Average current draw | 0.75A (12V)
Holding force between connectors | 60N
Overall dimensions (actuating part) | 40*40*20mm
Number of connecting positions | 12
Ability to change positions independently | Yes
Effective power | 5W
Power dissipation | 4W
Cost | 25$ USD
(a) SMORES [6] | (b) ATRON [24] | (c) MTRAN-III [9]
(d) Superbot [7] | (e) FreeBOT [1] | (f) NetSphere
Fig. 12. Different Designs of MSRR modules
| TABLE II
PERFORMANCE OF MSRR MODULES

Specification

SMORES
ATRON

MTRAN III
Superbot
Freebot

NetSphere

No. of DoF | 4 | 1 | 2 | 3 | 2 | 2
No. of Actuators | 5 | 6 | 5 | 9 | 2 | 1
Maximum Connecting No. | 4 | 8 | 6 | 6 | 12 | 30
Ability to Move Independently | Y | N | N | N | Y | N
Data Derived from | [6] | [24] | [9] | [7] | [1]

area as explained in section II.
Without using the corresponding drive system of motors, NetSphere realizes a simple structure which gives it great potential to reduce its volume. Moreover, because the actuating system occupies a large portion of space inside the module, NetSphere can achieve stronger power that other MSRRs with the same size.

VII. CONCLUSION AND FUTURE WORK
This paper proposes a novel MSRR design NetSphere, which utilizes innovative actuating and docking mechanism. The design has two versions with different advantages. Both of them
are capable of multiple tasks like connection and separation between modules, system reconfiguration and movement. The system formed by NetSphere is more flexible than previous MSRR because each module can actuate plenty of connectors simultaneously.
This paper is only a theorical design with some very basic experiment to test its feasibility. Some details of the design may not be the optimal choice. For example, the number of electromagnets and connectors on each circle orbit, even the structure of electromagnets we choose for the sphere. However, the key thought of this paper is to directly use electromagnets instead of motors to actuate the system in order to simplify the structure inside the module and improve the flexibility.
In our future work, the complete prototype for both versions of NetSphere will be implemented, and experiments based on the prototypes to test the connection and separation between modules, system reconfiguration and movement will be carried out. The relative localization and motion planning algorithm will be studied in the future as well.

REFERENCES

[1] G. Liang, H. Luo, M. Li, H. Qian, and T. Lam, “Freebot: A freeform modular self-reconfigurable robot with arbitrary connection point -design and implementation,” in IEEE International Conference on Robotics and Automation, 2020.
[2] Li Zhu, “A distributed modular self-reconfiguring robotic platform based on simplified electro-permanent magnets”, PhD manuscript, University of Toulouse, February 2018.
[3] P. Thalamy, B. Piranda, F. Lassabe, and J. Bourgeois. “Scaffold-Based Asynchronous Distributed Self-Reconfiguration By Continuous Module Flow”. In 2019 IEEE/RSJ International Conference on Intelligent Robots and Systems (IROS), pages 4840–4846, November 2019.
[4] Pierre Thalamy, Benoˆıt Piranda, Fred´ eric Lassabe, and Julien Bour-´ geois. “Deterministic scaffold assembly by self-reconfiguring microrobotic swarms”. Swarm and Evolutionary Computation, 58:100722, 2020.
[5] Pierre Thalamy, Benoˆıt Piranda, and Julien Bourgeois. “A survey of
autonomous | self-reconfiguration | methods | for | robot-based
programmable matter”. Robotics and Autonomous Systems, 120:103242, October 2019.
[6] J. Davey, N. Kwok, and M. Yim, “Emulating self-reconfigurable robots-design of the smores system,” in IEEE/RSJ International Conference on Intelligent Robots and Systems, 2012, pp. 4464–4469.
[7] B. Salemi, M. Moll, and W.-M. Shen, “Superbot: A deployable, multi-functional, and modular self-reconfigurable robotic system,” in IEEE/RSJ International Conference on Intelligent Robots and Systems, 2006, pp. 3636–3641.
[8] M. Yim, D.G. Duff, and K.D. Roufas. PolyBot: a modular reconfigurable robot. In Robotics and Automation, 2000. Proceedings. ICRA ’00. IEEE International Conference on, volume 1, pages 514 –520 vol.1, 2000.
[9] H. Kurokawa, K. Tomita, A. Kamimura, S. Kokaji, T. Hasuo, and S. Murata, “Distributed self-reconfiguration of m-tran iii modular robotic system,” The International Journal of Robotics Research, vol. 27, no. 3-4, pp. 373–386, 2008.
[10] A. Kamimura, H. Kurokawa, E. Yoshida, K. Tomita, S. Kokaji, and S. Murata, “Distributed adaptive locomotion by a modular robotic system, m-tran ii,” in IEEE/RSJ International Conference on Intelligent Robots and Systems, vol. 3, 2004, pp. 2370–2377.
[11] H. Wei, Y. Chen, J. Tan, and T. Wang, “Sambot: A self-assembly modular robot system,” IEEE/ASME Transactions on Mechatronics, vol. 16, no. 4, pp. 745–757, 2010.
[12] A. Sprowitz, S. Pouya, S. Bonardi, J. Van Den Kieboom, R. M ¨ ockel, ¨ A. Billard, P. Dillenbourg, and A. J. Ijspeert, “Roombots: reconfigurable robots for adaptive furniture,” IEEE Computational Intelligence Magazine, vol. 5, no. 3, pp. 20–32, 2010.
[13] J. W. Romanishin, K. Gilpin, S. Claici, and D. Rus, “3d m-blocks: Self-reconfiguring robots capable of locomotion via pivoting in three dimensions,” in IEEE International Conference on Robotics and Automation, 2015, pp. 1925–1932.
[14] G.Prasad, N.Sree Ramya, P.V.N.Prasad and G.Tulasi Ram Das, “Modelling and Simulation Analysis of the Brushless DC Motor by using MATLAB”, Int. J. Innov. Tech. Exp. Eng. 1(5), 27–31 (2012)
[15] J. Liedke and H. Worn, “Cobold-a bonding mechanism for modular ¨ self-reconfigurable mobile robots,” in IEEE International Conference on Robotics and Biomimetics, 2011, pp. 2025–2030.
[16] A. Kamimura, H. Kurokawa, E. Yoshida, K. Tomita, S. Kokaji, and S. Murata, “Distributed adaptive locomotion by a modular robotic system, m-tran ii,” in IEEE/RSJ International Conference on Intelligent Robots and Systems, vol. 3, 2004, pp. 2370–2377.
[17] K. Kotay, D. Rus, M. Vona, and C. McGray, “The self-reconfiguring robotic molecule,” in IEEE International Conference on Robotics and Automation, vol. 1, 1998, pp. 424–431.
[18] T. Tosun, J. Davey, C. Liu, and M. Yim, “Design and characterization of the ep-face connector,” in IEEE/RSJ International Conference on Intelligent Robots and Systems, 2016, pp. 45–51.
[19] N. Eckenstein and M. Yim, “Area of acceptance for 3d self-aligning robotic connectors: Concepts, metrics, and designs,” in IEEE International Conference on Robotics and Automation, 2014, pp. 1227–1233.
[20] Alchan Yun, Deaho Moon, Junhyoung Ha, Sungchul Kang, and Woosub Lee, “ModMan: An Advanced Reconfigurable Manipulator System With Genderless Connector and Automatic Kinematic Modeling Algorithm” in IEEE Robotics and Automation Letters (vol.5, Issue: 3, July 2020)
[21] D. Saldana, B. Gabrich, G. Li, M. Yim, and V. Kumar, “Modquad: The flying modular structure that self-assembles in midair,” in IEEE International Conference on Robotics and Automation, 2018, pp. 691– 698.
[22] J. W. Romanishin, K. Gilpin, and D. Rus, “M-blocks: Momentum-driven, magnetic modular robots,” in IEEE/RSJ International Conference on Intelligent Robots and Systems, 2013, pp. 4288–4295.
[23] R. Moreno, F. Veenstra, D. Silvera, J. Franco, O. Gracia, E. Cordoba, J. Gomez, and A. Faina, “Automated reconfiguration of modular robots using robot manipulators,” in 2018 IEEE Symposium Series on Computational Intelligence (SSCI). IEEE, 2018, pp. 884–891.
[24] M. W. Jorgensen, E. H. Ostergaard, and H. H. Lund, “Modular atron: Modules for a self-reconfigurable robot,” in IEEE/RSJ International Conference on Intelligent Robots and Systems, vol. 2, 2004, pp. 2068– 2073.

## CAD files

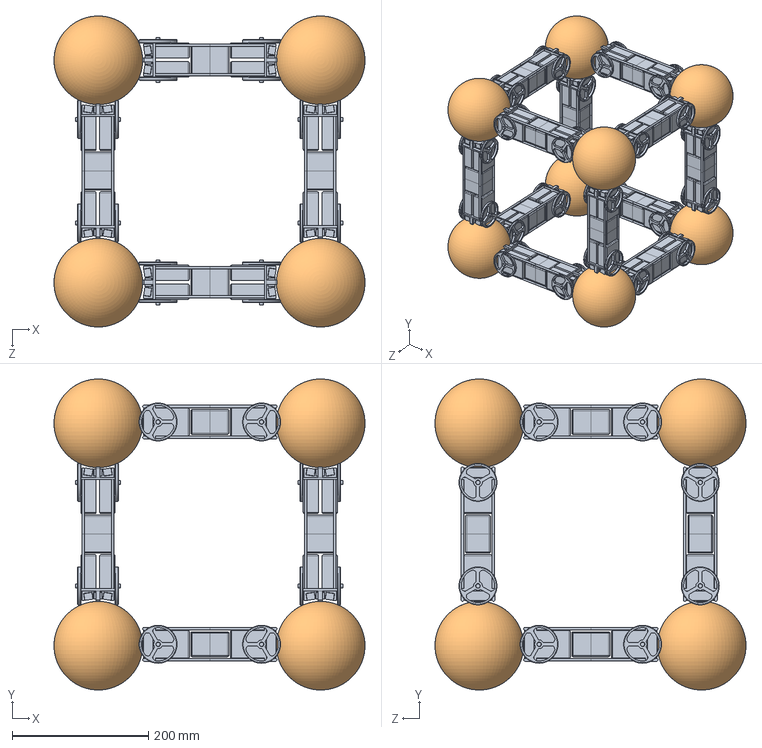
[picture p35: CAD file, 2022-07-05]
Solidworks_files/holistic_structure_2.SLDASM
456.0 x 456.0 x 456.0 mm
prototype01 x 24
球模型 x 8

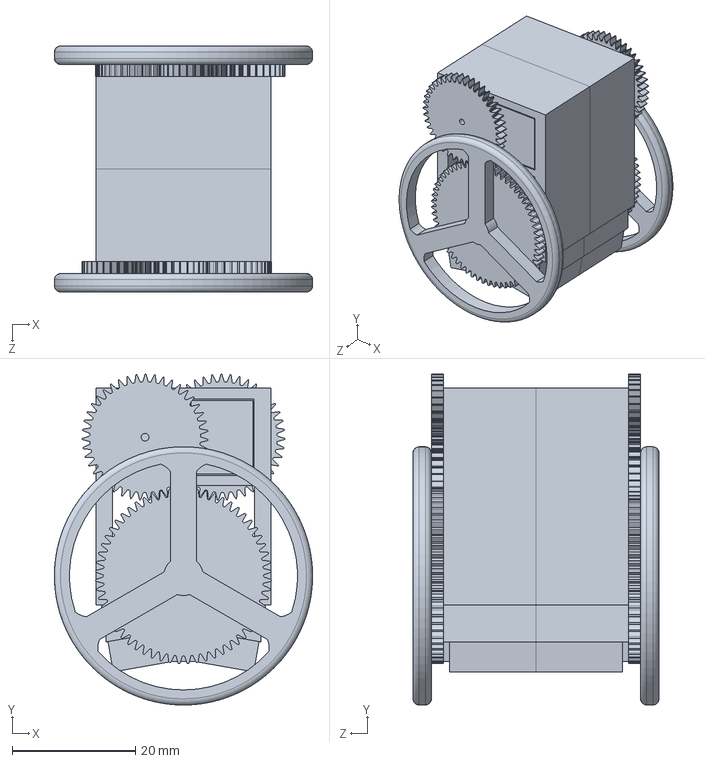
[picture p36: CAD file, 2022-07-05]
Solidworks_files/connecting_module_6.SLDASM
42.0 x 53.8 x 40.0 mm
new_33 x 2

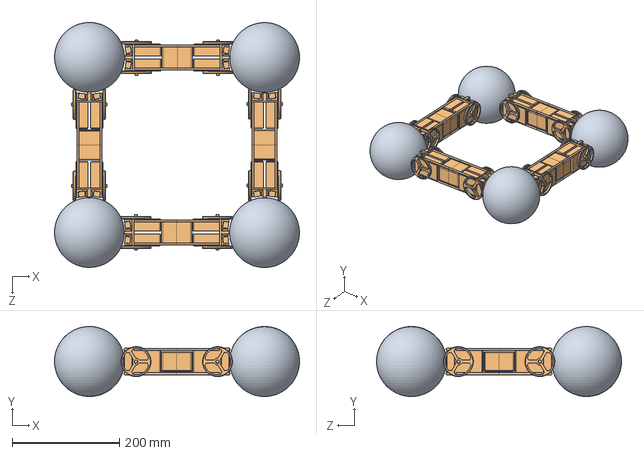
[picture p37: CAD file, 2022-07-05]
Solidworks_files/holistic_structure_1.SLDASM
456.2 x 130.4 x 456.2 mm
球模型 x 4
prototype01 x 8

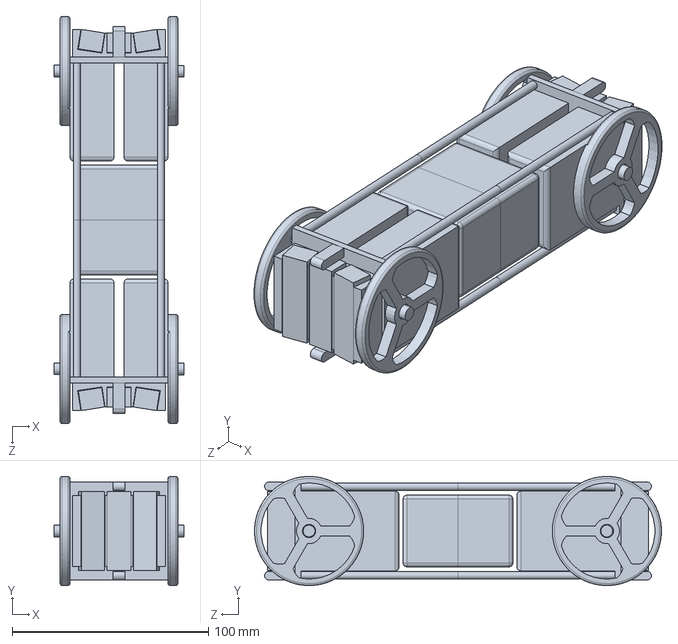
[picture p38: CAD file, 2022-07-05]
Solidworks_files/prototype_full.SLDASM
66.0 x 55.6 x 207.4 mm
prototype01 x 2

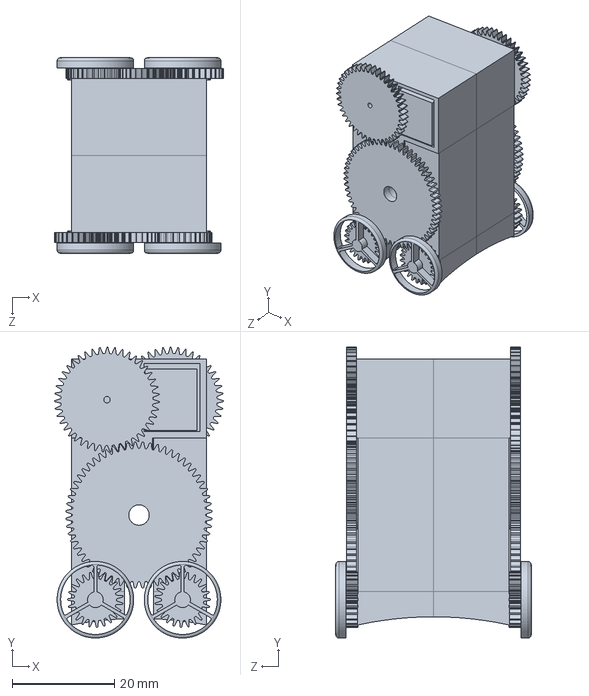
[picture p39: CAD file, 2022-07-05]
Solidworks_files/connecting_module_1.SLDASM
33.0 x 56.8 x 38.2 mm
new_73 x 2

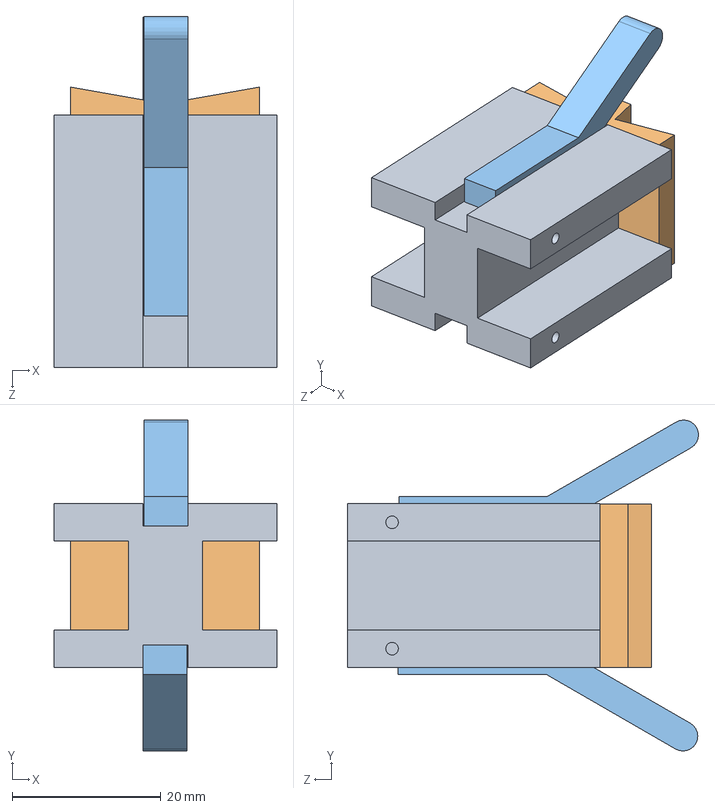
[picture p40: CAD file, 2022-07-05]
Solidworks_files/printing_part_1.SLDASM
30.0 x 44.5 x 47.2 mm
支架1
支架5
支架8 x 2

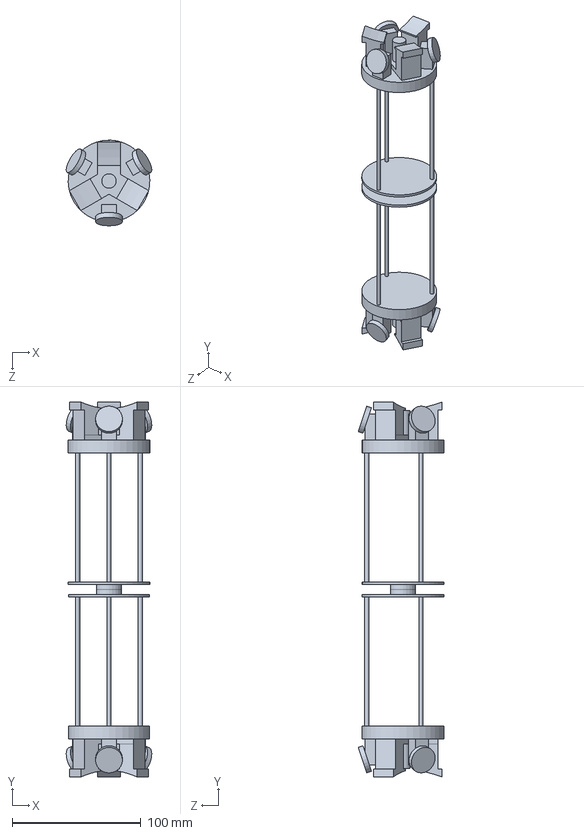
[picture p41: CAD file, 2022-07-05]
Solidworks_files/omniwheel_full.SLDASM
66.4 x 291.0 x 66.5 mm
3全向轮 x 2

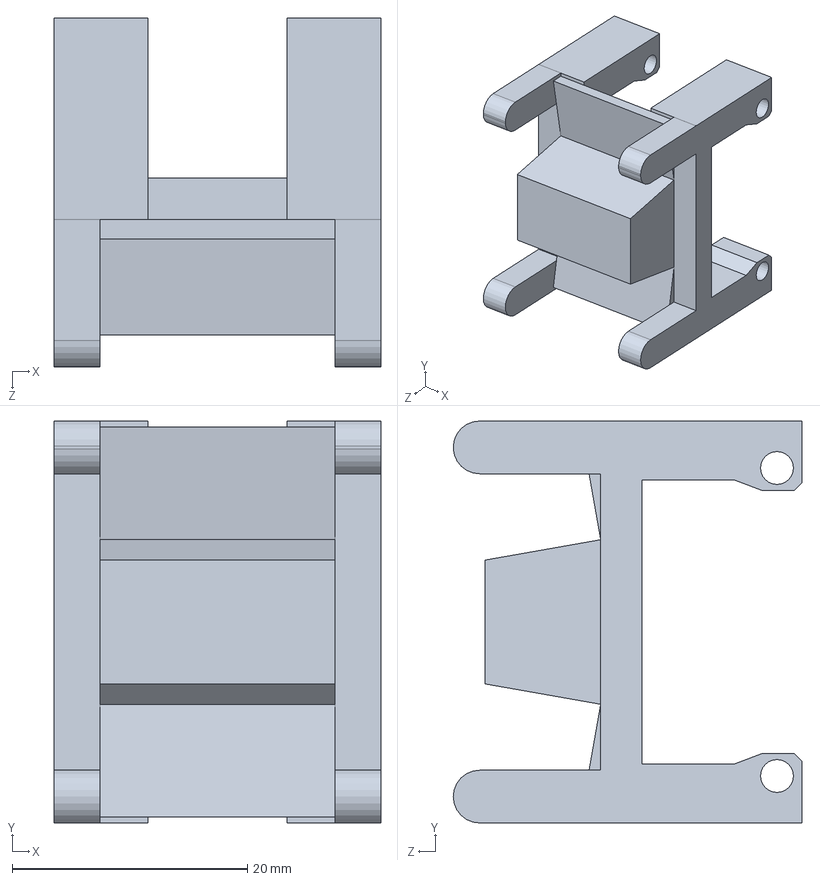
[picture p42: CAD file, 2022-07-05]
Solidworks_files/printing_part_2.SLDPRT
27.8 x 34.2 x 29.7 mm

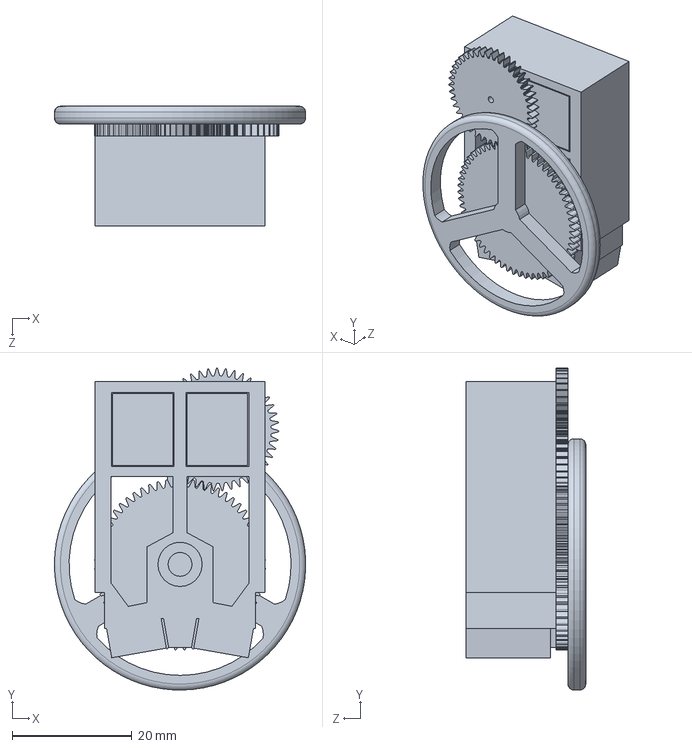
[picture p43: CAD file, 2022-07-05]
Solidworks_files/connecting_module_2.SLDPRT
42.0 x 53.8 x 20.0 mm

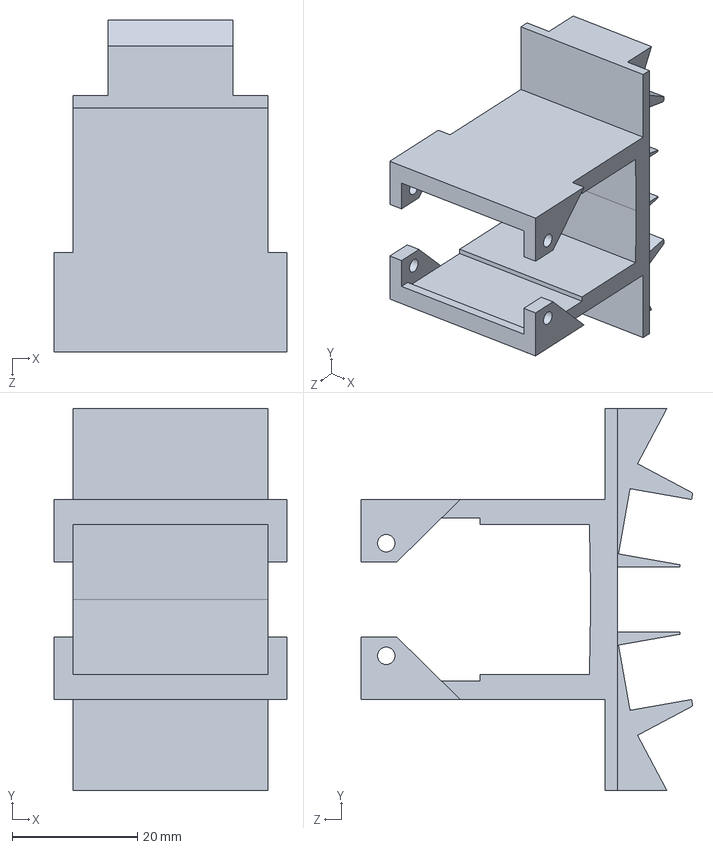
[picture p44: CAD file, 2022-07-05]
Solidworks_files/printing_part_4.SLDPRT
37.2 x 61.1 x 53.0 mm

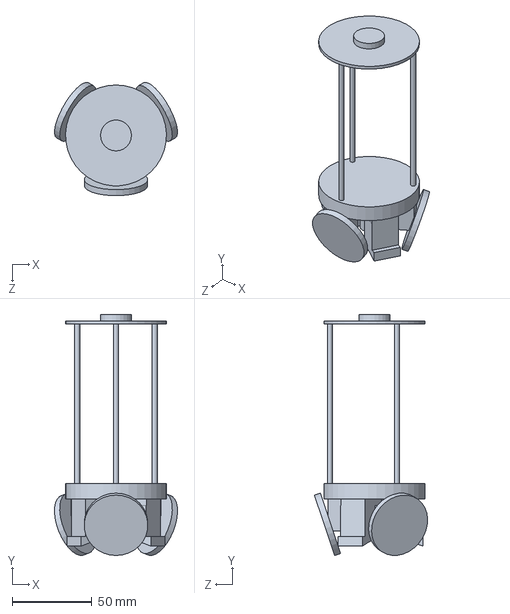
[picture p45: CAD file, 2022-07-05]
Solidworks_files/omniwheel_half.SLDPRT
77.3 x 151.4 x 71.2 mm

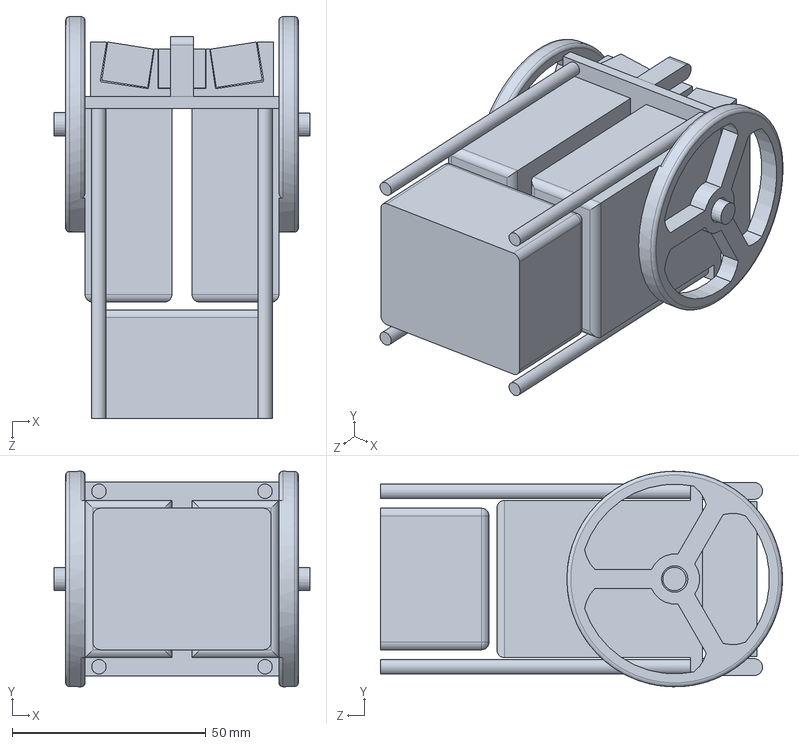
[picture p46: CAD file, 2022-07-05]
Solidworks_files/prototype_half.SLDPRT
66.0 x 55.6 x 103.7 mm

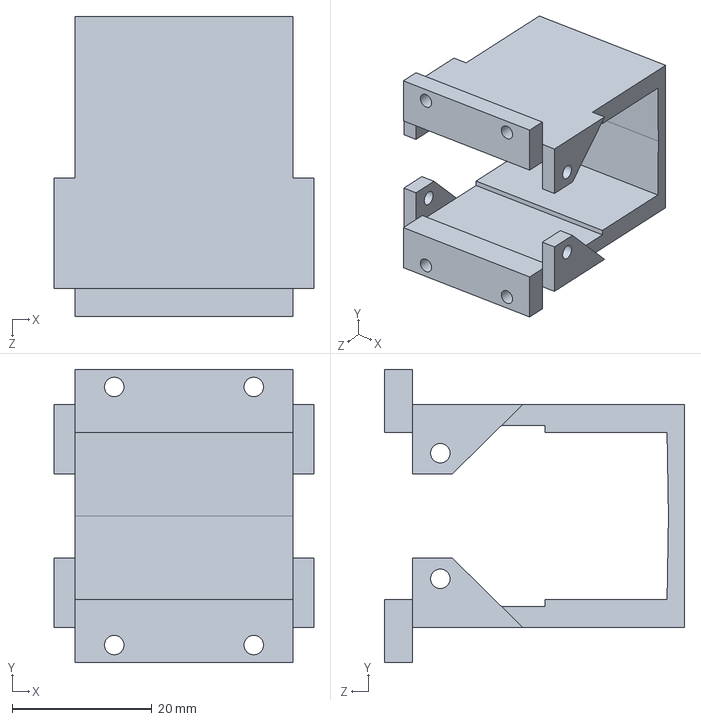
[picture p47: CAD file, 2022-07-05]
Solidworks_files/printing_part_3.SLDPRT
37.2 x 42.0 x 43.0 mm

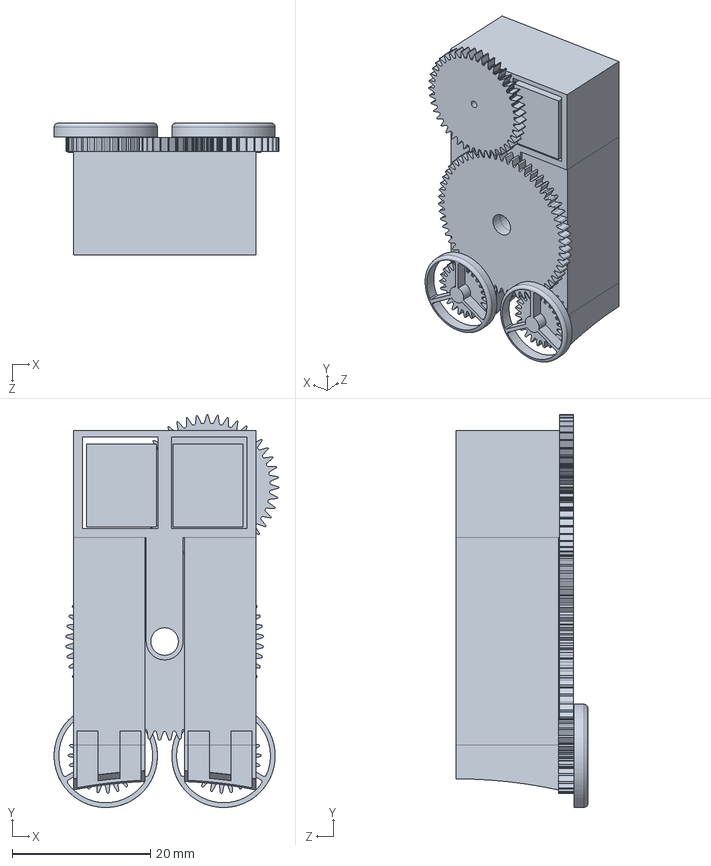
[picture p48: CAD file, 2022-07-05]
Solidworks_files/connecting_module_5.SLDPRT
32.5 x 56.8 x 19.1 mm

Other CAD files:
Solidworks_files/connecting_module_4.SLDPRT
Solidworks_files/connecting_module_3.SLDPRT

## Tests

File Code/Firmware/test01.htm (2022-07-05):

# Static Call Graph for image D:\keil_lib\test01\test01.axf

#<CALLGRAPH># ARM Linker, 5.02 [Build 28]: Last Updated: Mon Aug 12 09:33:49 2019

### Maximum Stack Usage = 320 bytes + Unknown(Functions without stacksize, Cycles, Untraceable Function Pointers)

### Call chain for Maximum Stack Depth:

_printf_f ⇒ _printf_fp_dec ⇒ _printf_fp_dec_real ⇒ _fp_digits ⇒ _btod_etento ⇒ _btod_emul ⇒ _e2e

### Functions with no stack information

- __user_initial_stackheap

### Mutually Recursive functions

- ADC1_2_IRQHandler ⇒ ADC1_2_IRQHandler
- HardFault_Handler ⇒ HardFault_Handler
- MemManage_Handler ⇒ MemManage_Handler
- BusFault_Handler ⇒ BusFault_Handler
- UsageFault_Handler ⇒ UsageFault_Handler

### Function Pointers

- ADC1_2_IRQHandler from startup_stm32f10x_hd.o(.text) referenced from startup_stm32f10x_hd.o(RESET)
- ADC3_IRQHandler from startup_stm32f10x_hd.o(.text) referenced from startup_stm32f10x_hd.o(RESET)
- BusFault_Handler from stm32f10x_it.o(.text) referenced from startup_stm32f10x_hd.o(RESET)
- CAN1_RX1_IRQHandler from startup_stm32f10x_hd.o(.text) referenced from startup_stm32f10x_hd.o(RESET)
- CAN1_SCE_IRQHandler from startup_stm32f10x_hd.o(.text) referenced from startup_stm32f10x_hd.o(RESET)
- DMA1_Channel1_IRQHandler from startup_stm32f10x_hd.o(.text) referenced from startup_stm32f10x_hd.o(RESET)
- DMA1_Channel2_IRQHandler from startup_stm32f10x_hd.o(.text) referenced from startup_stm32f10x_hd.o(RESET)
- DMA1_Channel3_IRQHandler from startup_stm32f10x_hd.o(.text) referenced from startup_stm32f10x_hd.o(RESET)
- DMA1_Channel4_IRQHandler from startup_stm32f10x_hd.o(.text) referenced from startup_stm32f10x_hd.o(RESET)
- DMA1_Channel5_IRQHandler from startup_stm32f10x_hd.o(.text) referenced from startup_stm32f10x_hd.o(RESET)
- DMA1_Channel6_IRQHandler from startup_stm32f10x_hd.o(.text) referenced from startup_stm32f10x_hd.o(RESET)
- DMA1_Channel7_IRQHandler from startup_stm32f10x_hd.o(.text) referenced from startup_stm32f10x_hd.o(RESET)
- DMA2_Channel1_IRQHandler from startup_stm32f10x_hd.o(.text) referenced from startup_stm32f10x_hd.o(RESET)
- DMA2_Channel2_IRQHandler from startup_stm32f10x_hd.o(.text) referenced from startup_stm32f10x_hd.o(RESET)
- DMA2_Channel3_IRQHandler from startup_stm32f10x_hd.o(.text) referenced from startup_stm32f10x_hd.o(RESET)
- DMA2_Channel4_5_IRQHandler from startup_stm32f10x_hd.o(.text) referenced from startup_stm32f10x_hd.o(RESET)
- DebugMon_Handler from stm32f10x_it.o(.text) referenced from startup_stm32f10x_hd.o(RESET)
- EXTI0_IRQHandler from startup_stm32f10x_hd.o(.text) referenced from startup_stm32f10x_hd.o(RESET)
- EXTI15_10_IRQHandler from startup_stm32f10x_hd.o(.text) referenced from startup_stm32f10x_hd.o(RESET)
- EXTI1_IRQHandler from startup_stm32f10x_hd.o(.text) referenced from startup_stm32f10x_hd.o(RESET)
- EXTI2_IRQHandler from startup_stm32f10x_hd.o(.text) referenced from startup_stm32f10x_hd.o(RESET)
- EXTI3_IRQHandler from startup_stm32f10x_hd.o(.text) referenced from startup_stm32f10x_hd.o(RESET)
- EXTI4_IRQHandler from startup_stm32f10x_hd.o(.text) referenced from startup_stm32f10x_hd.o(RESET)
- EXTI9_5_IRQHandler from startup_stm32f10x_hd.o(.text) referenced from startup_stm32f10x_hd.o(RESET)
- FLASH_IRQHandler from startup_stm32f10x_hd.o(.text) referenced from startup_stm32f10x_hd.o(RESET)
- FSMC_IRQHandler from startup_stm32f10x_hd.o(.text) referenced from startup_stm32f10x_hd.o(RESET)
- HardFault_Handler from stm32f10x_it.o(.text) referenced from startup_stm32f10x_hd.o(RESET)
- I2C1_ER_IRQHandler from startup_stm32f10x_hd.o(.text) referenced from startup_stm32f10x_hd.o(RESET)
- I2C1_EV_IRQHandler from startup_stm32f10x_hd.o(.text) referenced from startup_stm32f10x_hd.o(RESET)
- I2C2_ER_IRQHandler from startup_stm32f10x_hd.o(.text) referenced from startup_stm32f10x_hd.o(RESET)
- I2C2_EV_IRQHandler from startup_stm32f10x_hd.o(.text) referenced from startup_stm32f10x_hd.o(RESET)
- MemManage_Handler from stm32f10x_it.o(.text) referenced from startup_stm32f10x_hd.o(RESET)
- NMI_Handler from stm32f10x_it.o(.text) referenced from startup_stm32f10x_hd.o(RESET)
- PVD_IRQHandler from startup_stm32f10x_hd.o(.text) referenced from startup_stm32f10x_hd.o(RESET)
- PendSV_Handler from stm32f10x_it.o(.text) referenced from startup_stm32f10x_hd.o(RESET)
- RCC_IRQHandler from startup_stm32f10x_hd.o(.text) referenced from startup_stm32f10x_hd.o(RESET)
- RTCAlarm_IRQHandler from startup_stm32f10x_hd.o(.text) referenced from startup_stm32f10x_hd.o(RESET)
- RTC_IRQHandler from startup_stm32f10x_hd.o(.text) referenced from startup_stm32f10x_hd.o(RESET)
- Reset_Handler from startup_stm32f10x_hd.o(.text) referenced from startup_stm32f10x_hd.o(RESET)
- SDIO_IRQHandler from startup_stm32f10x_hd.o(.text) referenced from startup_stm32f10x_hd.o(RESET)
- SPI1_IRQHandler from startup_stm32f10x_hd.o(.text) referenced from startup_stm32f10x_hd.o(RESET)
- SPI2_IRQHandler from startup_stm32f10x_hd.o(.text) referenced from startup_stm32f10x_hd.o(RESET)
- SPI3_IRQHandler from startup_stm32f10x_hd.o(.text) referenced from startup_stm32f10x_hd.o(RESET)
- SVC_Handler from stm32f10x_it.o(.text) referenced from startup_stm32f10x_hd.o(RESET)
- SysTick_Handler from stm32f10x_it.o(.text) referenced from startup_stm32f10x_hd.o(RESET)
- SystemInit from system_stm32f10x.o(.text) referenced from startup_stm32f10x_hd.o(.text)
- TAMPER_IRQHandler from startup_stm32f10x_hd.o(.text) referenced from startup_stm32f10x_hd.o(RESET)
- TIM1_BRK_IRQHandler from startup_stm32f10x_hd.o(.text) referenced from startup_stm32f10x_hd.o(RESET)
- TIM1_CC_IRQHandler from startup_stm32f10x_hd.o(.text) referenced from startup_stm32f10x_hd.o(RESET)
- TIM1_TRG_COM_IRQHandler from startup_stm32f10x_hd.o(.text) referenced from startup_stm32f10x_hd.o(RESET)
- TIM1_UP_IRQHandler from startup_stm32f10x_hd.o(.text) referenced from startup_stm32f10x_hd.o(RESET)
- TIM2_IRQHandler from startup_stm32f10x_hd.o(.text) referenced from startup_stm32f10x_hd.o(RESET)
- TIM3_IRQHandler from startup_stm32f10x_hd.o(.text) referenced from startup_stm32f10x_hd.o(RESET)
- TIM4_IRQHandler from timer.o(.text) referenced from startup_stm32f10x_hd.o(RESET)
- TIM5_IRQHandler from startup_stm32f10x_hd.o(.text) referenced from startup_stm32f10x_hd.o(RESET)
- TIM6_IRQHandler from startup_stm32f10x_hd.o(.text) referenced from startup_stm32f10x_hd.o(RESET)
- TIM7_IRQHandler from startup_stm32f10x_hd.o(.text) referenced from startup_stm32f10x_hd.o(RESET)
- TIM8_BRK_IRQHandler from startup_stm32f10x_hd.o(.text) referenced from startup_stm32f10x_hd.o(RESET)
- TIM8_CC_IRQHandler from startup_stm32f10x_hd.o(.text) referenced from startup_stm32f10x_hd.o(RESET)
- TIM8_TRG_COM_IRQHandler from startup_stm32f10x_hd.o(.text) referenced from startup_stm32f10x_hd.o(RESET)
- TIM8_UP_IRQHandler from startup_stm32f10x_hd.o(.text) referenced from startup_stm32f10x_hd.o(RESET)
- UART4_IRQHandler from startup_stm32f10x_hd.o(.text) referenced from startup_stm32f10x_hd.o(RESET)
- UART5_IRQHandler from startup_stm32f10x_hd.o(.text) referenced from startup_stm32f10x_hd.o(RESET)
- USART1_IRQHandler from usart.o(.text) referenced from startup_stm32f10x_hd.o(RESET)
- USART2_IRQHandler from startup_stm32f10x_hd.o(.text) referenced from startup_stm32f10x_hd.o(RESET)
- USART3_IRQHandler from usart3.o(.text) referenced from startup_stm32f10x_hd.o(RESET)
- USBWakeUp_IRQHandler from startup_stm32f10x_hd.o(.text) referenced from startup_stm32f10x_hd.o(RESET)
- USB_HP_CAN1_TX_IRQHandler from startup_stm32f10x_hd.o(.text) referenced from startup_stm32f10x_hd.o(RESET)
- USB_LP_CAN1_RX0_IRQHandler from startup_stm32f10x_hd.o(.text) referenced from startup_stm32f10x_hd.o(RESET)
- UsageFault_Handler from stm32f10x_it.o(.text) referenced from startup_stm32f10x_hd.o(RESET)
- WWDG_IRQHandler from startup_stm32f10x_hd.o(.text) referenced from startup_stm32f10x_hd.o(RESET)
- __main from __main.o(!!!main) referenced from startup_stm32f10x_hd.o(.text)
- _get_lc_ctype from lc_ctype_c.o(locale$$code) referenced from rt_ctype_table.o(.text)
- _printf_input_char from _printf_char_common.o(.text) referenced from _printf_char_common.o(.text)
- _sputc from _sputc.o(.text) referenced from c89vsprintf.o(.text)

### Global Symbols

__main (Thumb, 8 bytes, Stack size 0 bytes, __main.o(!!!main))

[Calls]

- >> __rt_entry
- >> __scatterload

__scatterload (Thumb, 0 bytes, Stack size unknown bytes, __scatter.o(!!!scatter))

[Called By]

- >> __main

__scatterload_rt2 (Thumb, 44 bytes, Stack size unknown bytes, __scatter.o(!!!scatter), UNUSED)

[Calls]

- >> __rt_entry

__scatterload_rt2_thumb_only (Thumb, 0 bytes, Stack size unknown bytes, __scatter.o(!!!scatter), UNUSED)

__scatterload_null (Thumb, 0 bytes, Stack size unknown bytes, __scatter.o(!!!scatter), UNUSED)

__scatterload_copy (Thumb, 26 bytes, Stack size unknown bytes, __scatter_copy.o(!!handler_copy), UNUSED)

[Calls]

- >> __scatterload_copy

[Called By]

- >> __scatterload_copy

__scatterload_zeroinit (Thumb, 28 bytes, Stack size unknown bytes, __scatter_zi.o(!!handler_zi), UNUSED)

_printf_n (Thumb, 0 bytes, Stack size unknown bytes, _printf_n.o(.ARM.Collect$$_printf_percent$$00000001))

[Calls]

- >> _printf_charcount

_printf_percent (Thumb, 0 bytes, Stack size unknown bytes, _printf_percent.o(.ARM.Collect$$_printf_percent$$00000000))

[Called By]

- >> __printf

_printf_p (Thumb, 0 bytes, Stack size unknown bytes, _printf_p.o(.ARM.Collect$$_printf_percent$$00000002))

[Stack]

- Max Depth = 64 + Unknown Stack Size
- Call Chain = _printf_p ⇒ _printf_hex_ptr ⇒ _printf_longlong_hex ⇒ _printf_int_common ⇒ _printf_post_padding

[Calls]

- >> _printf_hex_ptr

_printf_f (Thumb, 0 bytes, Stack size unknown bytes, _printf_f.o(.ARM.Collect$$_printf_percent$$00000003))

[Stack]

- Max Depth = 320 + Unknown Stack Size
- Call Chain = _printf_f ⇒ _printf_fp_dec ⇒ _printf_fp_dec_real ⇒ _fp_digits ⇒ _btod_etento ⇒ _btod_emul ⇒ _e2e

[Calls]

- >> _printf_fp_dec

_printf_e (Thumb, 0 bytes, Stack size unknown bytes, _printf_e.o(.ARM.Collect$$_printf_percent$$00000004))

[Stack]

- Max Depth = 320 + Unknown Stack Size
- Call Chain = _printf_e ⇒ _printf_fp_dec ⇒ _printf_fp_dec_real ⇒ _fp_digits ⇒ _btod_etento ⇒ _btod_emul ⇒ _e2e

[Calls]

- >> _printf_fp_dec

_printf_g (Thumb, 0 bytes, Stack size unknown bytes, _printf_g.o(.ARM.Collect$$_printf_percent$$00000005))

[Stack]

- Max Depth = 320 + Unknown Stack Size
- Call Chain = _printf_g ⇒ _printf_fp_dec ⇒ _printf_fp_dec_real ⇒ _fp_digits ⇒ _btod_etento ⇒ _btod_emul ⇒ _e2e

[Calls]

- >> _printf_fp_dec

_printf_a (Thumb, 0 bytes, Stack size unknown bytes, _printf_a.o(.ARM.Collect$$_printf_percent$$00000006))

_printf_ll (Thumb, 0 bytes, Stack size unknown bytes, _printf_ll.o(.ARM.Collect$$_printf_percent$$00000007))

_printf_i (Thumb, 0 bytes, Stack size unknown bytes, _printf_i.o(.ARM.Collect$$_printf_percent$$00000008))

[Stack]

- Max Depth = 72 + Unknown Stack Size
- Call Chain = _printf_i ⇒ _printf_int_dec ⇒ _printf_int_common ⇒ _printf_post_padding

[Calls]

- >> _printf_int_dec

_printf_d (Thumb, 0 bytes, Stack size unknown bytes, _printf_d.o(.ARM.Collect$$_printf_percent$$00000009))

[Stack]

- Max Depth = 72 + Unknown Stack Size
- Call Chain = _printf_d ⇒ _printf_int_dec ⇒ _printf_int_common ⇒ _printf_post_padding

[Calls]

- >> _printf_int_dec

_printf_u (Thumb, 0 bytes, Stack size unknown bytes, _printf_u.o(.ARM.Collect$$_printf_percent$$0000000A))

[Stack]

- Max Depth = 72 + Unknown Stack Size
- Call Chain = _printf_u ⇒ _printf_int_dec ⇒ _printf_int_common ⇒ _printf_post_padding

[Calls]

- >> _printf_int_dec

_printf_o (Thumb, 0 bytes, Stack size unknown bytes, _printf_o.o(.ARM.Collect$$_printf_percent$$0000000B))

[Stack]

- Max Depth = 64 + Unknown Stack Size
- Call Chain = _printf_o ⇒ _printf_int_oct ⇒ _printf_longlong_oct ⇒ _printf_int_common ⇒ _printf_post_padding

[Calls]

- >> _printf_int_oct

_printf_x (Thumb, 0 bytes, Stack size unknown bytes, _printf_x.o(.ARM.Collect$$_printf_percent$$0000000C))

[Stack]

- Max Depth = 80 + Unknown Stack Size
- Call Chain = _printf_x ⇒ _printf_int_hex ⇒ _printf_longlong_hex ⇒ _printf_int_common ⇒ _printf_post_padding

[Calls]

- >> _printf_int_hex

_printf_lli (Thumb, 0 bytes, Stack size unknown bytes, _printf_lli.o(.ARM.Collect$$_printf_percent$$0000000D))

[Stack]

- Max Depth = 72 + Unknown Stack Size
- Call Chain = _printf_lli ⇒ _printf_longlong_dec ⇒ _printf_int_common ⇒ _printf_post_padding

[Calls]

- >> _printf_longlong_dec

_printf_lld (Thumb, 0 bytes, Stack size unknown bytes, _printf_lld.o(.ARM.Collect$$_printf_percent$$0000000E))

[Stack]

- Max Depth = 72 + Unknown Stack Size
- Call Chain = _printf_lld ⇒ _printf_longlong_dec ⇒ _printf_int_common ⇒ _printf_post_padding

[Calls]

- >> _printf_longlong_dec

_printf_llu (Thumb, 0 bytes, Stack size unknown bytes, _printf_llu.o(.ARM.Collect$$_printf_percent$$0000000F))

[Stack]

- Max Depth = 72 + Unknown Stack Size
- Call Chain = _printf_llu ⇒ _printf_longlong_dec ⇒ _printf_int_common ⇒ _printf_post_padding

[Calls]

- >> _printf_longlong_dec

_printf_llo (Thumb, 0 bytes, Stack size unknown bytes, _printf_llo.o(.ARM.Collect$$_printf_percent$$00000010))

[Stack]

- Max Depth = 56 + Unknown Stack Size
- Call Chain = _printf_llo ⇒ _printf_ll_oct ⇒ _printf_longlong_oct ⇒ _printf_int_common ⇒ _printf_post_padding

[Calls]

- >> _printf_ll_oct

_printf_llx (Thumb, 0 bytes, Stack size unknown bytes, _printf_llx.o(.ARM.Collect$$_printf_percent$$00000011))

[Stack]

- Max Depth = 64 + Unknown Stack Size
- Call Chain = _printf_llx ⇒ _printf_ll_hex ⇒ _printf_longlong_hex ⇒ _printf_int_common ⇒ _printf_post_padding

[Calls]

- >> _printf_ll_hex

_printf_l (Thumb, 0 bytes, Stack size unknown bytes, _printf_l.o(.ARM.Collect$$_printf_percent$$00000012))

_printf_c (Thumb, 0 bytes, Stack size unknown bytes, _printf_c.o(.ARM.Collect$$_printf_percent$$00000013))

[Stack]

- Max Depth = 40 + Unknown Stack Size
- Call Chain = _printf_c ⇒ _printf_char ⇒ _printf_cs_common ⇒ _printf_str ⇒ _printf_post_padding

[Calls]

- >> _printf_char

_printf_s (Thumb, 0 bytes, Stack size unknown bytes, _printf_s.o(.ARM.Collect$$_printf_percent$$00000014))

[Stack]

- Max Depth = 40 + Unknown Stack Size
- Call Chain = _printf_s ⇒ _printf_string ⇒ _printf_cs_common ⇒ _printf_str ⇒ _printf_post_padding

[Calls]

- >> _printf_string

_printf_lc (Thumb, 0 bytes, Stack size unknown bytes, _printf_lc.o(.ARM.Collect$$_printf_percent$$00000015))

[Stack]

- Max Depth = 88 + Unknown Stack Size
- Call Chain = _printf_lc ⇒ _printf_wchar ⇒ _printf_lcs_common ⇒ _printf_wctomb ⇒ _wcrtomb ⇒ __rt_ctype_table

[Calls]

- >> _printf_wchar

_printf_ls (Thumb, 0 bytes, Stack size unknown bytes, _printf_ls.o(.ARM.Collect$$_printf_percent$$00000016))

[Stack]

- Max Depth = 88 + Unknown Stack Size
- Call Chain = _printf_ls ⇒ _printf_wstring ⇒ _printf_lcs_common ⇒ _printf_wctomb ⇒ _wcrtomb ⇒ __rt_ctype_table

[Calls]

- >> _printf_wstring

_printf_percent_end (Thumb, 0 bytes, Stack size unknown bytes, _printf_percent_end.o(.ARM.Collect$$_printf_percent$$00000017))

__rt_lib_init (Thumb, 0 bytes, Stack size unknown bytes, libinit.o(.ARM.Collect$$libinit$$00000000))

[Called By]

- >> __rt_entry_li

__rt_lib_init_fp_1 (Thumb, 0 bytes, Stack size unknown bytes, libinit2.o(.ARM.Collect$$libinit$$00000002))

__rt_lib_init_heap_1 (Thumb, 0 bytes, Stack size unknown bytes, libinit2.o(.ARM.Collect$$libinit$$00000008))

__rt_lib_init_lc_common (Thumb, 0 bytes, Stack size unknown bytes, libinit2.o(.ARM.Collect$$libinit$$0000000D))

[Calls]

- >> __rt_locale

__rt_lib_init_rand_1 (Thumb, 0 bytes, Stack size unknown bytes, libinit2.o(.ARM.Collect$$libinit$$0000000C))

__rt_lib_init_user_alloc_1 (Thumb, 0 bytes, Stack size unknown bytes, libinit2.o(.ARM.Collect$$libinit$$0000000A))

__rt_lib_init_lc_collate_1 (Thumb, 0 bytes, Stack size unknown bytes, libinit2.o(.ARM.Collect$$libinit$$0000000F))

__rt_lib_init_lc_ctype_2 (Thumb, 0 bytes, Stack size unknown bytes, libinit2.o(.ARM.Collect$$libinit$$00000010))

[Stack]

- Max Depth = 8 + Unknown Stack Size
- Call Chain = __rt_lib_init_lc_ctype_2 ⇒ _get_lc_ctype

[Calls]

- >> _get_lc_ctype

__rt_lib_init_lc_ctype_1 (Thumb, 0 bytes, Stack size unknown bytes, libinit2.o(.ARM.Collect$$libinit$$00000011))

__rt_lib_init_lc_monetary_1 (Thumb, 0 bytes, Stack size unknown bytes, libinit2.o(.ARM.Collect$$libinit$$00000013))

__rt_lib_init_lc_numeric_2 (Thumb, 0 bytes, Stack size unknown bytes, libinit2.o(.ARM.Collect$$libinit$$00000014))

[Stack]

- Max Depth = 8 + Unknown Stack Size
- Call Chain = __rt_lib_init_lc_numeric_2 ⇒ _get_lc_numeric

[Calls]

- >> _get_lc_numeric

__rt_lib_init_alloca_1 (Thumb, 0 bytes, Stack size unknown bytes, libinit2.o(.ARM.Collect$$libinit$$0000002C))

__rt_lib_init_argv_1 (Thumb, 0 bytes, Stack size unknown bytes, libinit2.o(.ARM.Collect$$libinit$$0000002A))

__rt_lib_init_atexit_1 (Thumb, 0 bytes, Stack size unknown bytes, libinit2.o(.ARM.Collect$$libinit$$00000019))

__rt_lib_init_clock_1 (Thumb, 0 bytes, Stack size unknown bytes, libinit2.o(.ARM.Collect$$libinit$$0000001F))

__rt_lib_init_cpp_1 (Thumb, 0 bytes, Stack size unknown bytes, libinit2.o(.ARM.Collect$$libinit$$00000030))

__rt_lib_init_exceptions_1 (Thumb, 0 bytes, Stack size unknown bytes, libinit2.o(.ARM.Collect$$libinit$$0000002E))

__rt_lib_init_fp_trap_1 (Thumb, 0 bytes, Stack size unknown bytes, libinit2.o(.ARM.Collect$$libinit$$0000001D))

__rt_lib_init_getenv_1 (Thumb, 0 bytes, Stack size unknown bytes, libinit2.o(.ARM.Collect$$libinit$$00000021))

__rt_lib_init_lc_numeric_1 (Thumb, 0 bytes, Stack size unknown bytes, libinit2.o(.ARM.Collect$$libinit$$00000015))

__rt_lib_init_lc_time_1 (Thumb, 0 bytes, Stack size unknown bytes, libinit2.o(.ARM.Collect$$libinit$$00000017))

__rt_lib_init_return (Thumb, 0 bytes, Stack size unknown bytes, libinit2.o(.ARM.Collect$$libinit$$00000031))

__rt_lib_init_signal_1 (Thumb, 0 bytes, Stack size unknown bytes, libinit2.o(.ARM.Collect$$libinit$$0000001B))

__rt_lib_init_stdio_1 (Thumb, 0 bytes, Stack size unknown bytes, libinit2.o(.ARM.Collect$$libinit$$00000023))

__rt_lib_shutdown (Thumb, 0 bytes, Stack size unknown bytes, libshutdown.o(.ARM.Collect$$libshutdown$$00000000))

[Called By]

- >> __rt_exit_ls

__rt_lib_shutdown_fp_trap_1 (Thumb, 0 bytes, Stack size unknown bytes, libshutdown2.o(.ARM.Collect$$libshutdown$$00000006))

__rt_lib_shutdown_heap_1 (Thumb, 0 bytes, Stack size unknown bytes, libshutdown2.o(.ARM.Collect$$libshutdown$$0000000E))

__rt_lib_shutdown_return (Thumb, 0 bytes, Stack size unknown bytes, libshutdown2.o(.ARM.Collect$$libshutdown$$0000000F))

__rt_lib_shutdown_signal_1 (Thumb, 0 bytes, Stack size unknown bytes, libshutdown2.o(.ARM.Collect$$libshutdown$$00000009))

__rt_lib_shutdown_stdio_1 (Thumb, 0 bytes, Stack size unknown bytes, libshutdown2.o(.ARM.Collect$$libshutdown$$00000003))

__rt_lib_shutdown_user_alloc_1 (Thumb, 0 bytes, Stack size unknown bytes, libshutdown2.o(.ARM.Collect$$libshutdown$$0000000B))

__rt_entry (Thumb, 0 bytes, Stack size unknown bytes, rtentry.o(.ARM.Collect$$rtentry$$00000000))

[Called By]

- >> __main
- >> __scatterload_rt2

__rt_entry_presh_1 (Thumb, 0 bytes, Stack size unknown bytes, rtentry2.o(.ARM.Collect$$rtentry$$00000002))

__rt_entry_sh (Thumb, 0 bytes, Stack size unknown bytes, rtentry4.o(.ARM.Collect$$rtentry$$00000004))

[Stack]

- Max Depth = 8 + Unknown Stack Size
- Call Chain = __rt_entry_sh ⇒ __user_setup_stackheap

[Calls]

- >> __user_setup_stackheap

__rt_entry_li (Thumb, 0 bytes, Stack size unknown bytes, rtentry2.o(.ARM.Collect$$rtentry$$0000000A))

[Calls]

- >> __rt_lib_init

__rt_entry_postsh_1 (Thumb, 0 bytes, Stack size unknown bytes, rtentry2.o(.ARM.Collect$$rtentry$$00000009))

__rt_entry_main (Thumb, 0 bytes, Stack size unknown bytes, rtentry2.o(.ARM.Collect$$rtentry$$0000000D))

[Stack]

- Max Depth = 108 + Unknown Stack Size
- Call Chain = __rt_entry_main ⇒ main ⇒ initAll ⇒ usart3_init ⇒ TIM4_Int_Init ⇒ NVIC_Init

[Calls]

- >> main
- >> exit

__rt_entry_postli_1 (Thumb, 0 bytes, Stack size unknown bytes, rtentry2.o(.ARM.Collect$$rtentry$$0000000C))

__rt_exit (Thumb, 0 bytes, Stack size unknown bytes, rtexit.o(.ARM.Collect$$rtexit$$00000000))

[Called By]

- >> exit

__rt_exit_ls (Thumb, 0 bytes, Stack size unknown bytes, rtexit2.o(.ARM.Collect$$rtexit$$00000003))

[Calls]

- >> __rt_lib_shutdown

__rt_exit_prels_1 (Thumb, 0 bytes, Stack size unknown bytes, rtexit2.o(.ARM.Collect$$rtexit$$00000002))

__rt_exit_exit (Thumb, 0 bytes, Stack size unknown bytes, rtexit2.o(.ARM.Collect$$rtexit$$00000004))

[Calls]

- >> _sys_exit

Reset_Handler (Thumb, 8 bytes, Stack size 0 bytes, startup_stm32f10x_hd.o(.text))
[Address Reference Count : 1]

- startup_stm32f10x_hd.o(RESET)

ADC1_2_IRQHandler (Thumb, 0 bytes, Stack size 0 bytes, startup_stm32f10x_hd.o(.text))

[Calls]

- >> ADC1_2_IRQHandler

[Called By]

- >> ADC1_2_IRQHandler

[Address Reference Count : 1]

- startup_stm32f10x_hd.o(RESET)

ADC3_IRQHandler (Thumb, 0 bytes, Stack size 0 bytes, startup_stm32f10x_hd.o(.text))
[Address Reference Count : 1]

- startup_stm32f10x_hd.o(RESET)

CAN1_RX1_IRQHandler (Thumb, 0 bytes, Stack size 0 bytes, startup_stm32f10x_hd.o(.text))
[Address Reference Count : 1]

- startup_stm32f10x_hd.o(RESET)

CAN1_SCE_IRQHandler (Thumb, 0 bytes, Stack size 0 bytes, startup_stm32f10x_hd.o(.text))
[Address Reference Count : 1]

- startup_stm32f10x_hd.o(RESET)

DMA1_Channel1_IRQHandler (Thumb, 0 bytes, Stack size 0 bytes, startup_stm32f10x_hd.o(.text))
[Address Reference Count : 1]

- startup_stm32f10x_hd.o(RESET)

DMA1_Channel2_IRQHandler (Thumb, 0 bytes, Stack size 0 bytes, startup_stm32f10x_hd.o(.text))
[Address Reference Count : 1]

- startup_stm32f10x_hd.o(RESET)

DMA1_Channel3_IRQHandler (Thumb, 0 bytes, Stack size 0 bytes, startup_stm32f10x_hd.o(.text))
[Address Reference Count : 1]

- startup_stm32f10x_hd.o(RESET)

DMA1_Channel4_IRQHandler (Thumb, 0 bytes, Stack size 0 bytes, startup_stm32f10x_hd.o(.text))
[Address Reference Count : 1]

- startup_stm32f10x_hd.o(RESET)

DMA1_Channel5_IRQHandler (Thumb, 0 bytes, Stack size 0 bytes, startup_stm32f10x_hd.o(.text))
[Address Reference Count : 1]

- startup_stm32f10x_hd.o(RESET)

DMA1_Channel6_IRQHandler (Thumb, 0 bytes, Stack size 0 bytes, startup_stm32f10x_hd.o(.text))
[Address Reference Count : 1]

- startup_stm32f10x_hd.o(RESET)

DMA1_Channel7_IRQHandler (Thumb, 0 bytes, Stack size 0 bytes, startup_stm32f10x_hd.o(.text))
[Address Reference Count : 1]

- startup_stm32f10x_hd.o(RESET)

DMA2_Channel1_IRQHandler (Thumb, 0 bytes, Stack size 0 bytes, startup_stm32f10x_hd.o(.text))
[Address Reference Count : 1]

- startup_stm32f10x_hd.o(RESET)

DMA2_Channel2_IRQHandler (Thumb, 0 bytes, Stack size 0 bytes, startup_stm32f10x_hd.o(.text))
[Address Reference Count : 1]

- startup_stm32f10x_hd.o(RESET)

DMA2_Channel3_IRQHandler (Thumb, 0 bytes, Stack size 0 bytes, startup_stm32f10x_hd.o(.text))
[Address Reference Count : 1]

- startup_stm32f10x_hd.o(RESET)

DMA2_Channel4_5_IRQHandler (Thumb, 0 bytes, Stack size 0 bytes, startup_stm32f10x_hd.o(.text))
[Address Reference Count : 1]

- startup_stm32f10x_hd.o(RESET)

EXTI0_IRQHandler (Thumb, 0 bytes, Stack size 0 bytes, startup_stm32f10x_hd.o(.text))
[Address Reference Count : 1]

- startup_stm32f10x_hd.o(RESET)

EXTI15_10_IRQHandler (Thumb, 0 bytes, Stack size 0 bytes, startup_stm32f10x_hd.o(.text))
[Address Reference Count : 1]

- startup_stm32f10x_hd.o(RESET)

EXTI1_IRQHandler (Thumb, 0 bytes, Stack size 0 bytes, startup_stm32f10x_hd.o(.text))
[Address Reference Count : 1]

- startup_stm32f10x_hd.o(RESET)

EXTI2_IRQHandler (Thumb, 0 bytes, Stack size 0 bytes, startup_stm32f10x_hd.o(.text))
[Address Reference Count : 1]

- startup_stm32f10x_hd.o(RESET)

EXTI3_IRQHandler (Thumb, 0 bytes, Stack size 0 bytes, startup_stm32f10x_hd.o(.text))
[Address Reference Count : 1]

- startup_stm32f10x_hd.o(RESET)

EXTI4_IRQHandler (Thumb, 0 bytes, Stack size 0 bytes, startup_stm32f10x_hd.o(.text))
[Address Reference Count : 1]

- startup_stm32f10x_hd.o(RESET)
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

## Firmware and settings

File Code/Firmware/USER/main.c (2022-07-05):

#include "led.h"
#include "lee.h"
#include "delay.h"
#include "sys.h"
#include "usart.h"
#include "dht11.h" 	
#include "package.h"
#include "DL_LN3X.h"
#include "usart3.h"			 	 
#include "string.h"	  
#include <stdio.h>  

void recievePkg(sPkg* pkg);
void loopReceive(void);
void loopAll(void);
void initAll(void);
extern void uartRevieveByte(u8 data);

	u8 temperature;  	    
	u8 humidity;  

newPkg(3) redPkg={7,0x90,0x32,0x00,0x00,{0,10,20}};

char buf1[7]={0x05,0x90,0x21,0x00,0x00,0x01,0xFF}; 
char buf2[7]={0x05,0x90,0x21,0x00,0x00,0x02,0xFF}; 
char buf3[7]={0x05,0x90,0x21,0x00,0x00,0x03,0xFF}; 
char buf4[7]={0x05,0x90,0x21,0x00,0x00,0x04,0xFF}; 


newPkg(1) THPkg={5,0x90,0x32,0x01,0x00,{0}}; 

void loopAll()
{ 
	u16 i;
	u8 reclen=0;  
	u8 m=0;

	
	
	while (1)
	{
	
		THPkg.dis_port = 0xa0;
		THPkg.data[0] = 30;
		sendPkg((sPkg*)(&THPkg));

		for(i = 0;i<100;i++)
		{
			delay_ms(10);
			loopReceive();
		}		
		THPkg.dis_port = 0xa1;
		THPkg.data[0] = m;
		m++;
		if(m==0xff)m=0;
		sendPkg((sPkg*)(&THPkg));
		
		
			
		if(USART3_RX_STA&0X8000)			 
		 {

		   reclen=USART3_RX_STA&0X7FFF;	 
			 
			 for(i=0;i<reclen;i++)
			 uartRevieveByte(USART3_RX_BUF[i]);

			 USART3_RX_STA=0;	 
		 }

		for(i = 0;i<100;i++)
			{
				delay_ms(10);
				loopReceive();
			}		 
 									
	}
}

void loopReceive(void)
{
	sPkg* pkg;
	pkg = getNextPkg();
	while(pkg != NULL)
	{
		recievePkg(pkg);
		pkg = getNextPkg();
	}
}


void recievePkg(sPkg* pkg)
{
	
	switch(pkg->dis_port)
	{
		case 0xa0:		
		if(pkg->data[0] == 0x01)
		{
			
		LED0=!LED0; 
		}
		break;
		
		case 0xb0:		
		if(pkg->data[0] == 0x01)
		{

		LED1=!LED1; 
		}
		break;
		
		case 0xc0:		
		if(pkg->data[0] == 0x01)
		{
		LED2=!LED2; 
		}
		break;
		
		case 0xd0:		
		if(pkg->data[0] == 0x01)
		{

			GPIO_SetBits(GPIOA,GPIO_Pin_8);
    	GPIO_SetBits(GPIOA,GPIO_Pin_5);
	    GPIO_SetBits(GPIOA,GPIO_Pin_6);
		}
		break;
		
		default:
		break;		
	}
}


void initAll()
{

	delay_init();	    	  
	NVIC_PriorityGroupConfig(NVIC_PriorityGroup_2); 
	uart_init(115200);	  
	usart3_init(115200); 
	LED_Init();		  	  
	
	
	
}

 int main(void)
 {	


	initAll();
	loopAll();

}

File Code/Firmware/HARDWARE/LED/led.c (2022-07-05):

#include "led.h"

//////////////////////////////////////////////////////////////////////////////////	 
//本程序只供学习使用，未经作者许可，不得用于其它任何用途

//LED驱动代码	   

//All rights reserved									  
////////////////////////////////////////////////////////////////////////////////// 	   

//初始化PB12为输出口.并使能这个口的时钟		    
//LED IO初始化
void LED_Init(void)
{
 
 GPIO_InitTypeDef  GPIO_InitStructure;
 	
 RCC_APB2PeriphClockCmd(RCC_APB2Periph_GPIOB, ENABLE);	 //使能PB端口时钟
	
 GPIO_InitStructure.GPIO_Pin = GPIO_Pin_12;				 //LED0-->PB.12 端口配置
 GPIO_InitStructure.GPIO_Mode = GPIO_Mode_Out_PP; 		 //推挽输出
 GPIO_InitStructure.GPIO_Speed = GPIO_Speed_50MHz;		 //IO口速度为50MHz
 GPIO_Init(GPIOB, &GPIO_InitStructure);					 //根据设定参数初始化GPIOB.12
 GPIO_SetBits(GPIOB,GPIO_Pin_12);						 //PA.12 输出高


}
 

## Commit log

2022-07-05 code added
    [SKT文本记录2017年03月08日20-07-06.csv, SKT文本记录2017年03月08日20-10-53.csv, SKT文本记录2017年03月08日22-54-56.csv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]
2022-07-05 3d models added
    [connecting_module_1.SLDASM, connecting_module_2.SLDPRT, connecting_module_3.SLDPRT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]
